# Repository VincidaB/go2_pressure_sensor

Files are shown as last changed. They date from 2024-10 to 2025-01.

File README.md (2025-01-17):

The pressure sensor used is the GZP6859A040KPP33Z, as a replacement for the original XGZP6869A040 (Both have a pressure range between 0-40KPa).

The tube on the GO2 EDU is 1mm ID and 3mm OD silicone tubing, but I could make it fit on the pressure sensors, so I used 1.5mm ID instead. A small piece of tape or heat shrink can be used ont the foot side to make it fit better.

The screws needed are M2 length 4mm countersunk screws, the original being Philips head. 7 screws are needed per leg, for a total of 28 screws. They fix the tubing using two small plastic brackets than can be 3D printed, the files are in the `3d_models` folder (4 of each must be printed).

By removing a plastic cover on the inner part of the leg, a connector is revealed, which connects to the sensor once it has been fastened : 
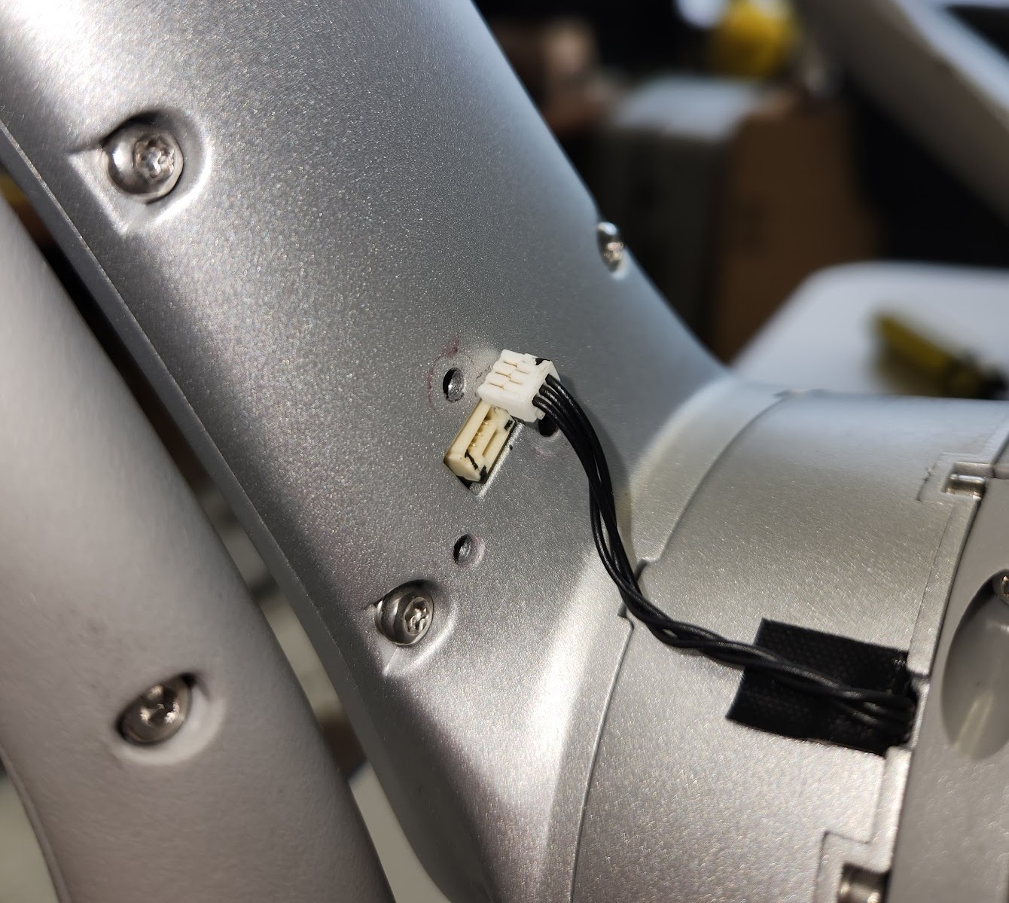
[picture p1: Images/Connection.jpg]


One of the 3D printed brackets, fastened, holding the tube in place:
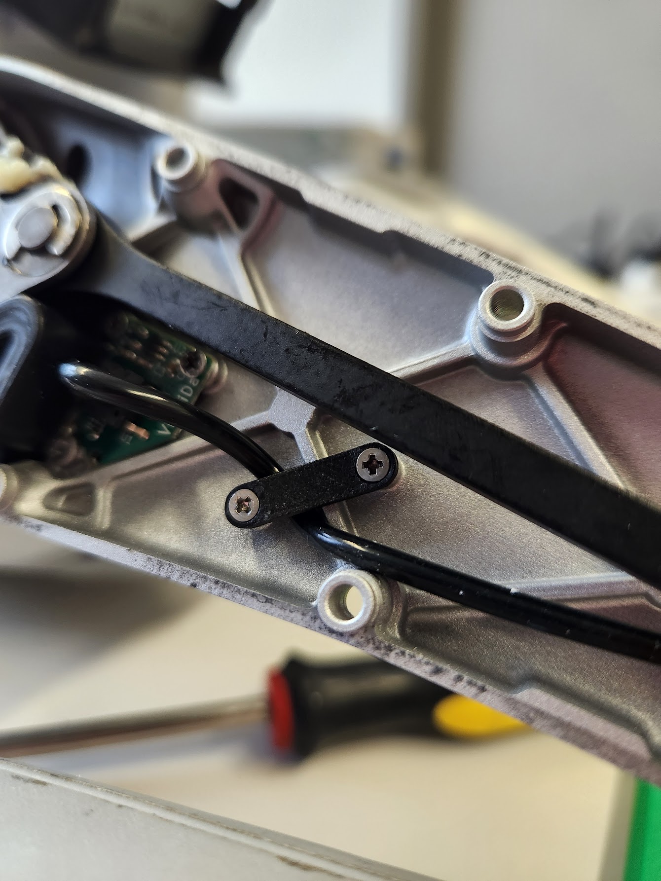
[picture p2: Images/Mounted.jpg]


Here is the final PCBs manufactured and assembled:
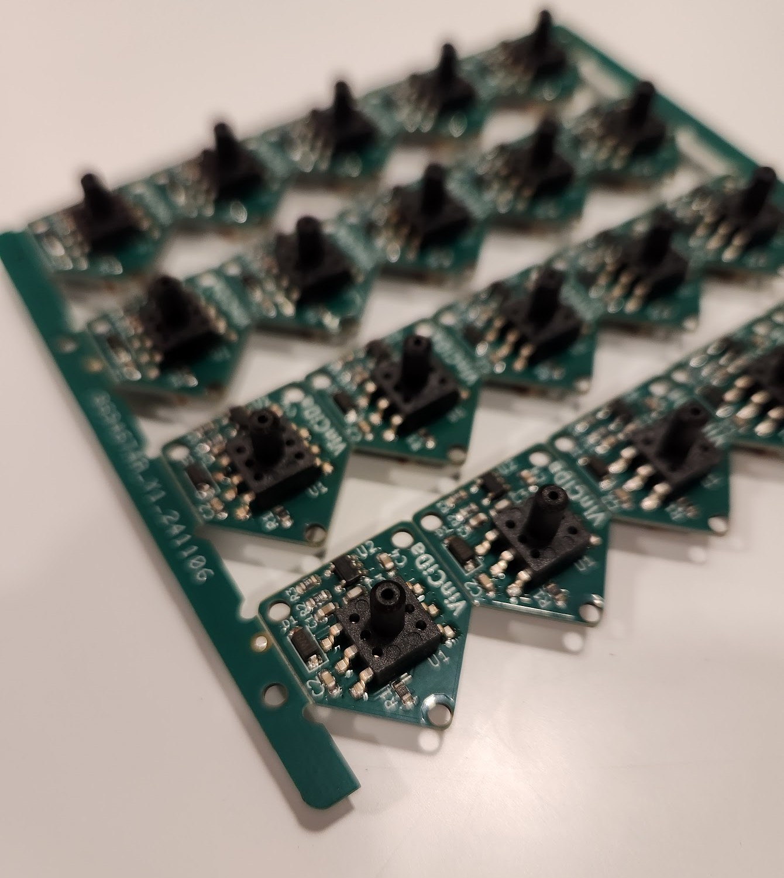
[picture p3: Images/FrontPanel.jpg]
Front view of the panel

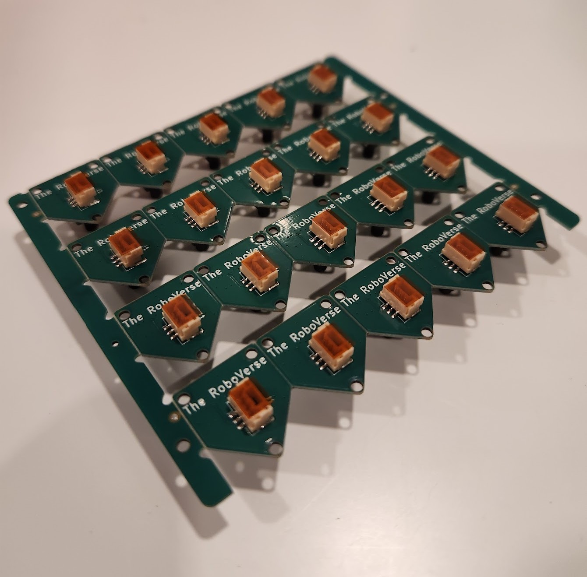
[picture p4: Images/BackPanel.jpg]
Back view of the panel


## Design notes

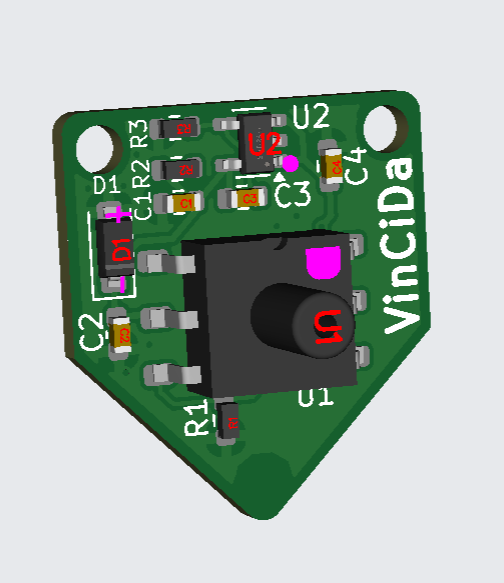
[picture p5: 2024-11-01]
Images/FrontJLCPCB.png

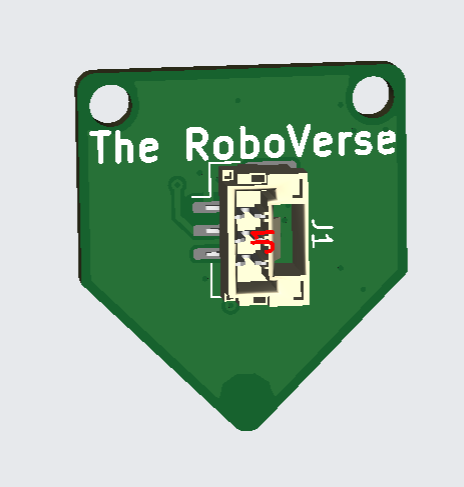
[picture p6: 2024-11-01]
Images/BackJLCPCB.png

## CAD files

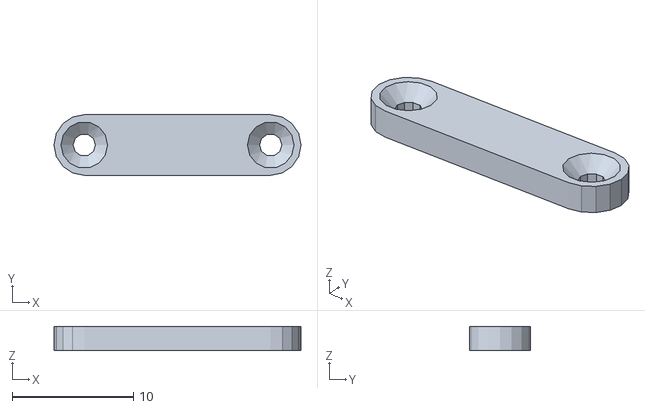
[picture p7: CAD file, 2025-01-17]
3d_models/BracketTube2.stl
20.4 x 5.00 x 2.00

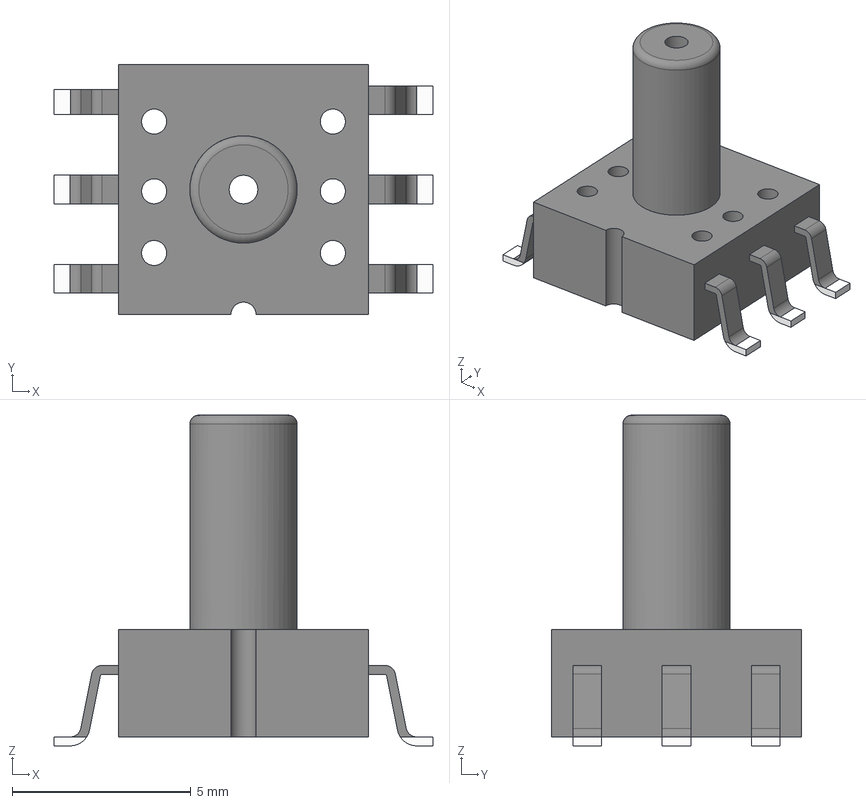
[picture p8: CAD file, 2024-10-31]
GZP6869 v6.step
10.6 x 7.00 x 9.25 mm

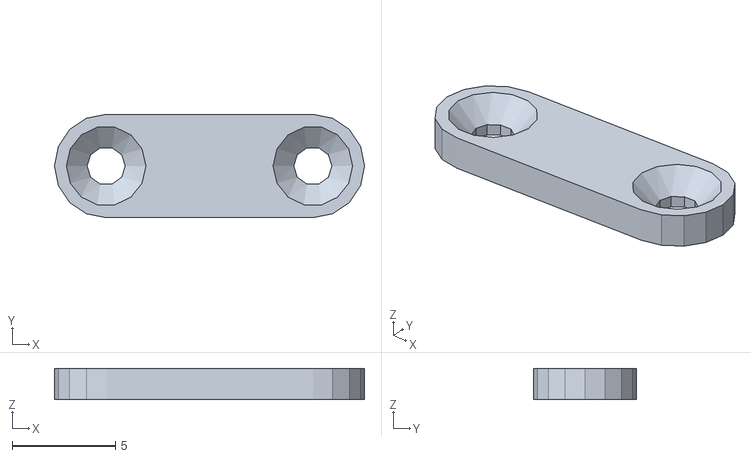
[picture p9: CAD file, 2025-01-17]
3d_models/BracketTube1.stl
15.0 x 5.00 x 1.50

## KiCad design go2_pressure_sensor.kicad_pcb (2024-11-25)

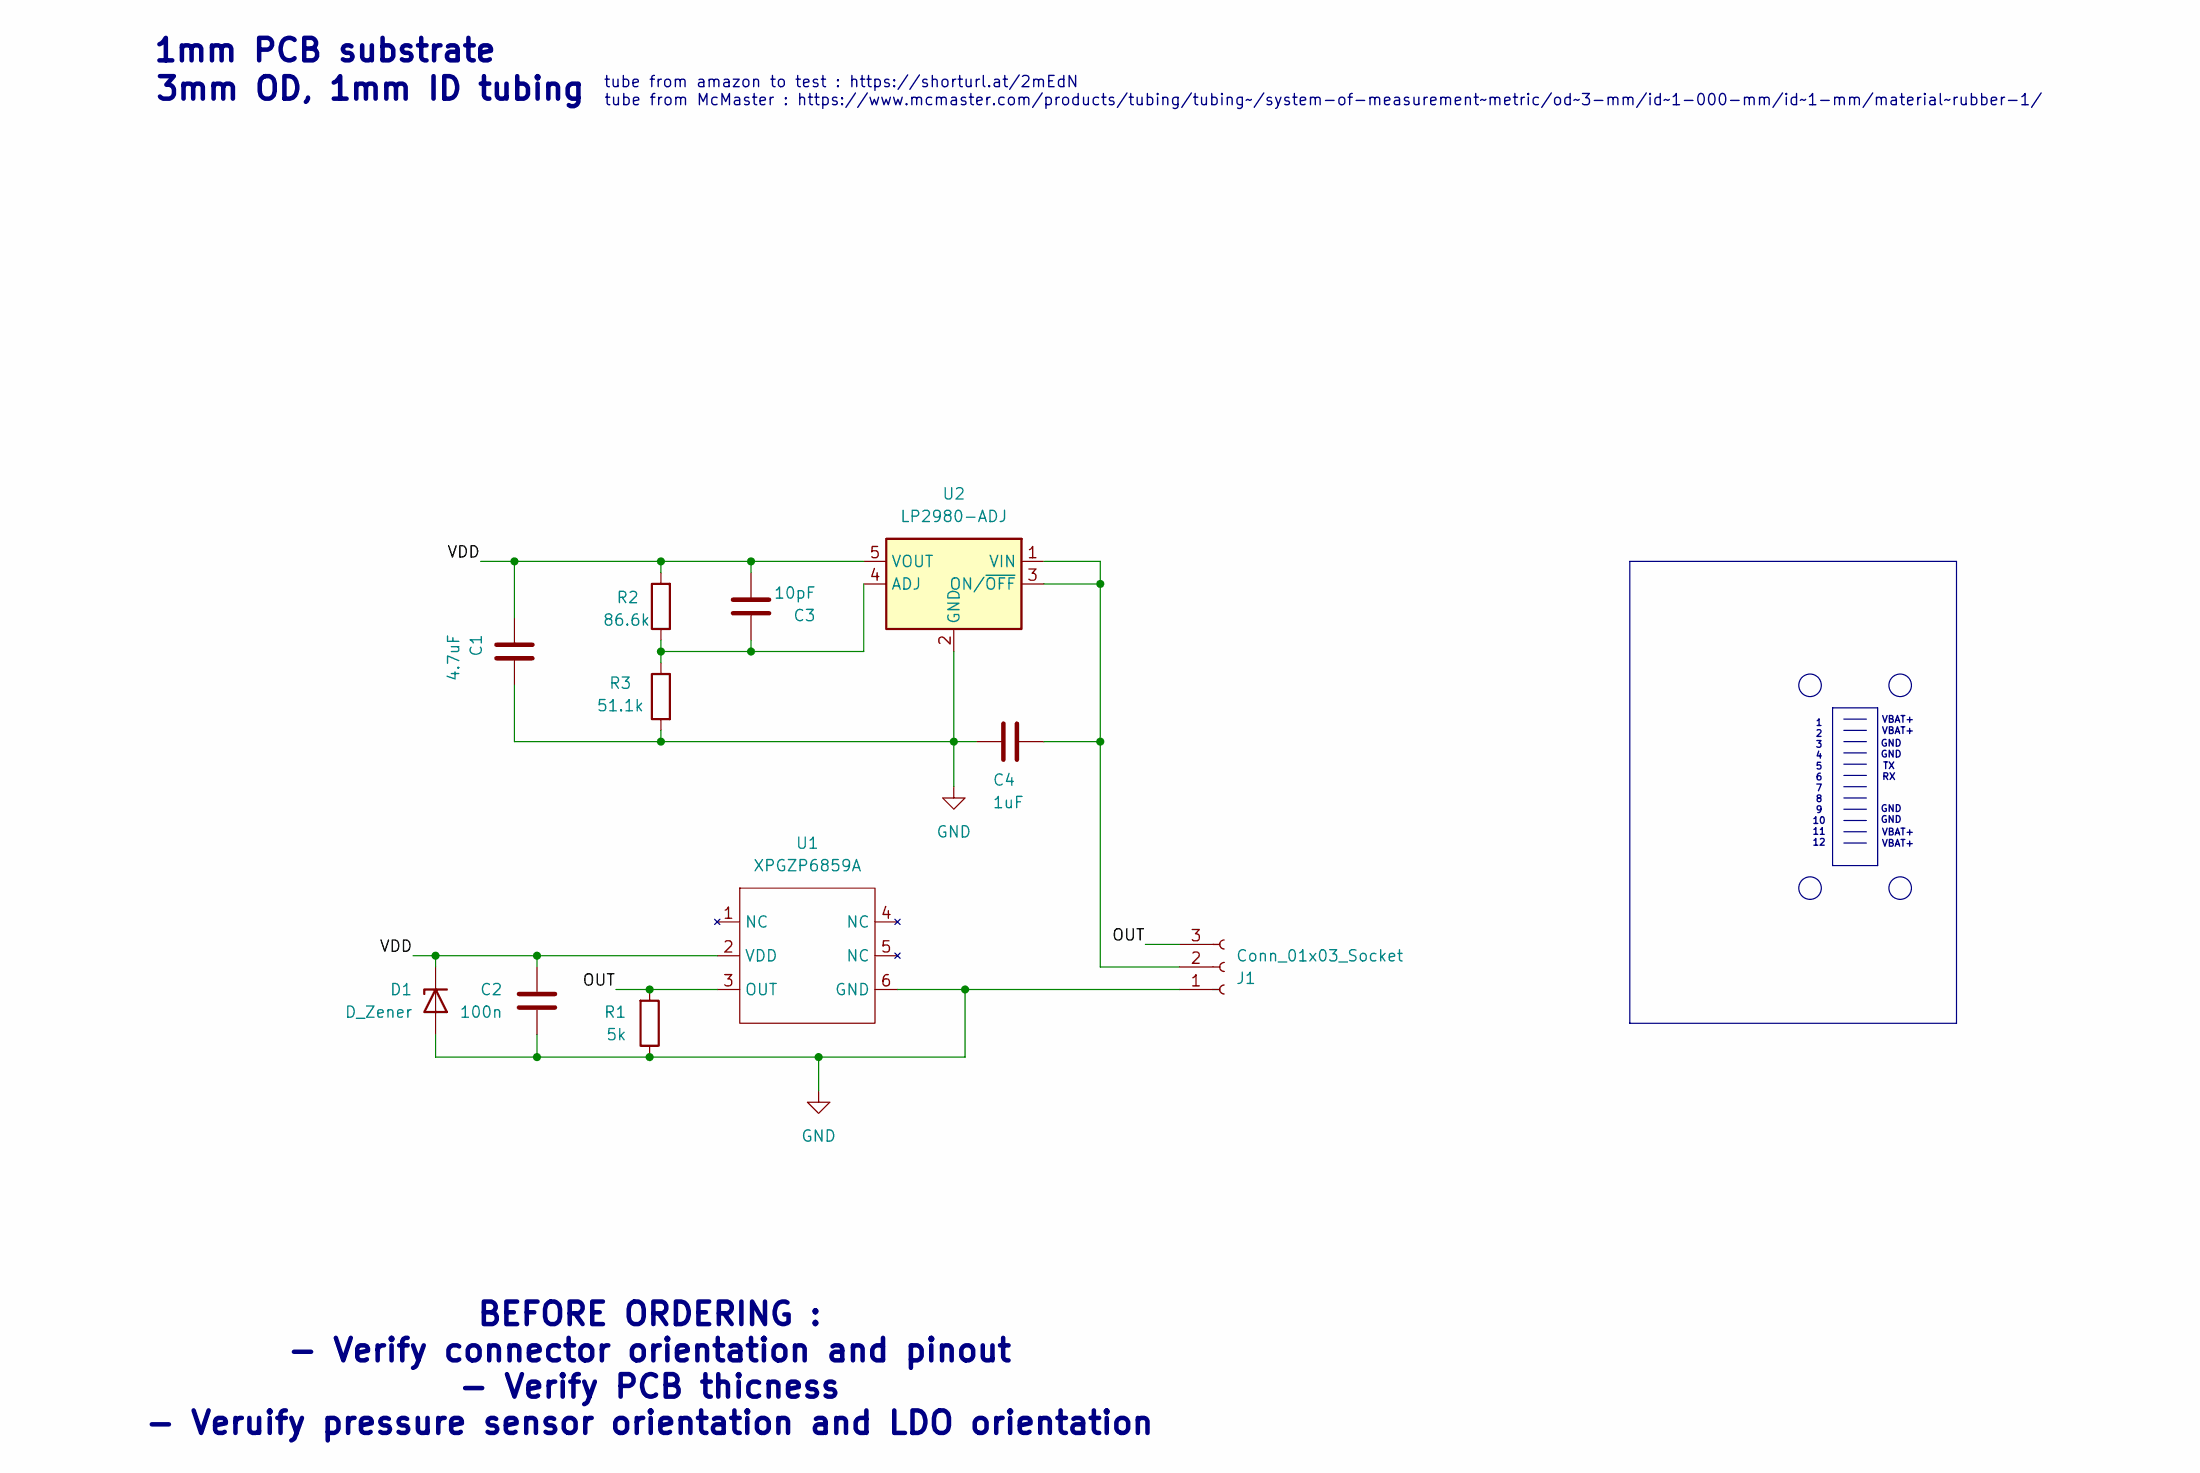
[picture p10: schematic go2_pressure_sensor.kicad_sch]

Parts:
C1: 4.7uF; R_0603_1608Metric; LCSC C19666
C2: 100n; C_0603_1608Metric; LCSC C66501
C3: 10pF; R_0603_1608Metric; LCSC C106245
C4: 1uF; R_0603_1608Metric; LCSC C6119849
D1: D_Zener; D_SOD-123; LCSC C2117
J1: Conn_01x03_Socket; JST_GH_BM03B-GHS-TBT_1x03-1MP_P1.25mm_Vertical; LCSC C161691
R1: 5k; R_0603_1608Metric; LCSC C2828621
R2: 86.6k; R_0603_1608Metric; LCSC C3000725
R3: 51.1k; R_0603_1608Metric; LCSC C2933234
U1: XPGZP6859A; XGZ6859 6pin; LCSC C3038019
U2: LP2980-ADJ; SOT-23-5; LCSC C181526

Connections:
/OUT: J1.3, R1.2, U1.3 (OUT)
/VDD: C1.2, C2.1, C3.1, D1.1 (K), R2.2, U1.2 (VDD), U2.5 (VOUT)
GND: C1.1, C2.2, C4.2, D1.2 (A), J1.1, R1.1, R3.2, U1.6 (GND), U2.2 (GND)
unnamed: C4.1, J1.2, U2.1 (VIN), U2.3 (ON/~OFF)
unnamed: C3.2, R2.1, R3.1, U2.4 (ADJ)

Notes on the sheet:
GND GND
BEFORE ORDERING : - Verify connector orientation and pinout - Verify PCB thicness - Veruify pressure sensor orientation and LDO orientation
1 2 3 4 5 6 7 8 9 10 11 12
1mm PCB substrate
VBAT+
3mm OD, 1mm ID tubing
tube from amazon to test : https://shorturl.at/2mEdN
tube from McMaster : https://www.mcmaster.com/products/tubing/tubing~/system-of-measurement~metric/od~3-mm/id~1-000-mm/id~1-mm/material~rubber-1/
TX RX

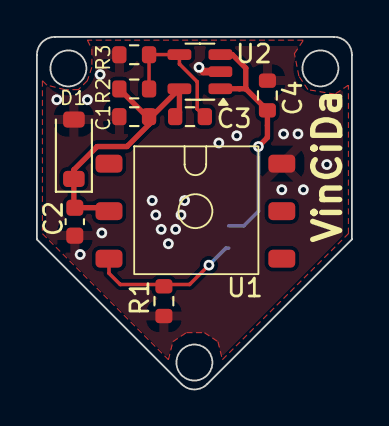
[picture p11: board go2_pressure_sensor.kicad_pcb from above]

Board: 2 copper layers, 17.5 x 19.6 mm, 11 parts (1 on the bottom side), 5 nets.

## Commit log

2024-10-30 init git repo
    [go2_pressure_sensor.kicad_pcb, go2_pressure_sensor.kicad_sch]
2024-10-30 Added datasheets for the potential and the current sensors
2024-10-30 Added connector diagram of the GO2 battery (unrelated)
    [go2_pressure_sensor.kicad_sch]
2024-10-31 Non verified version with new presure transducer
    [GZP6869 v6.step, go2_pressure_sensor.kicad_pcb, go2_pressure_sensor.kicad_sch]
2024-11-01 Removed copied sensors schematic
    [go2_pressure_sensor.kicad_pcb, go2_pressure_sensor.kicad_sch, go2_pressure_sensor.step]
2024-11-25 Added silkscreen markings for pressure sensor
    [go2_pressure_sensor.kicad_pcb, go2_pressure_sensor.kicad_sch]
2024-11-25 removed step model
    [go2_pressure_sensor.step]
2025-01-10 Update README.md to add pressure sensor part number
2025-01-17 Added more details to README
    [BracketTube1.stl, BracketTube2.stl]
